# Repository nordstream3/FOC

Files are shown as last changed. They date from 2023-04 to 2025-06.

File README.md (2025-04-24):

# King of FOC motor control hardware aka FOC_KING

## The DIY Open Source Vesc6 and FOC capable HW with onboard IMU and CAN
<div>


</div>

IMAGE ALT TEXT (https://www.youtube.com/watch?v=1HfkBNfPIXc "FreeDRIVE")

Date | Manufacturer | amount | includes | shipping & tax | price
| -------- | -------- | -------- | -------- | -------- | -------- |
2024-01-17 | JLCPCB | 10 boards | All assembled excl fets and caps | YES, to EU | $241.08

An open-source motor controller board based on a JLCPCB friendly [VESC6 75V/300A](https://vesc-project.com/sites/default/files/Benjamin%20Posts/vesc_75_300.pdf) so-called "driverless" design with individual gate drivers for all three phases. It is powered by an STM32F405 MCU and is capable of running FOC at high power and voltages.

A motor controller designed for FOC (Field Oriented Control) and HFI (High Frequency Injection), a sensorless teqnique enabling full torque at zero speed without sensor feedback. The hardware is separated in 3 sub-modules which are assembled using standard pin headers.

POWER BRIDGE | MCU | SUPPLY
|----|----|----|
 |  | 
3 phase power bridge | STM32F405 PILL | +12,+5V,+3V

Intended for "small" electric vehicles like Skateboards, OneWheels, Bicycles, Robotics, Boats, and is designed in sub-modules as a reference design for further development.

The standard design includes 12 mosfets, but it will also work with just 6 fets. You choose.

## Features
* 84V/200A continuous rating
* 20s battery voltage rating
* 3-phase FOC motor control
* 4-layer pcb design with individual gate drivers for all three phases
* STM32F405 MCU
* USB-C
* CAN, 5 mbps
* Onboard IMU (Bosch BMI270)
* Momentary on/off switch connection via 4-pin jst connector
* Led data pin for programmable LEDs
* Compact design with fets mounted on the bottom side
* 12V for gate drivers, 5V for CAN and IMU, and 3.3V for MCU and op-amped current-sense amplification
* Cheap and up-to-date with cheapest and **well stocked** components available for ordering at [JLCPCB](https://jlcpcb.com/) and [LCSC](https://www.lcsc.com)
* **Dimensions of assembled board: 65 x 78 mm**

<div>
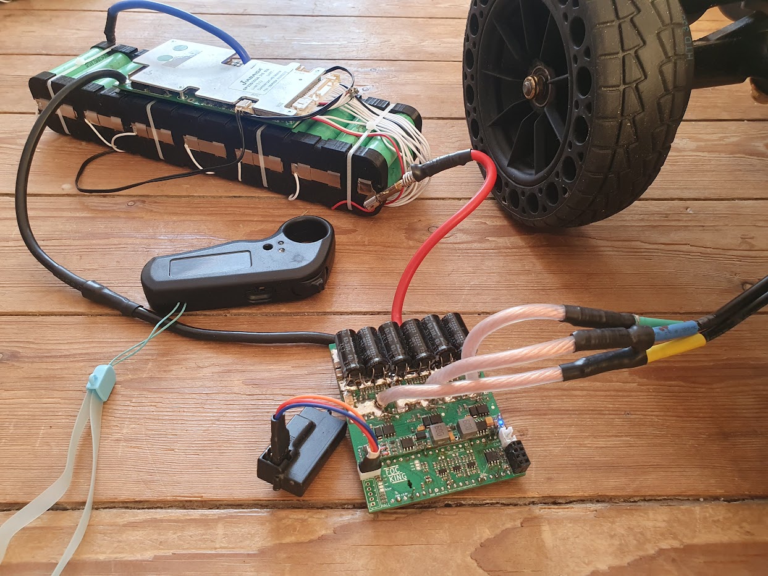
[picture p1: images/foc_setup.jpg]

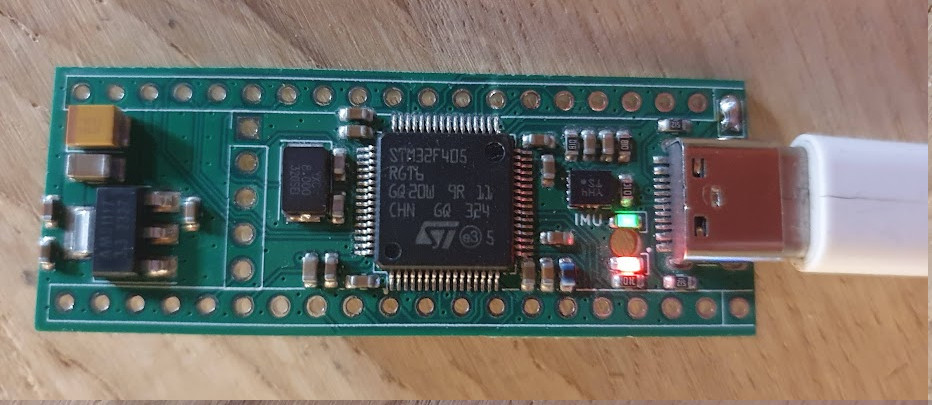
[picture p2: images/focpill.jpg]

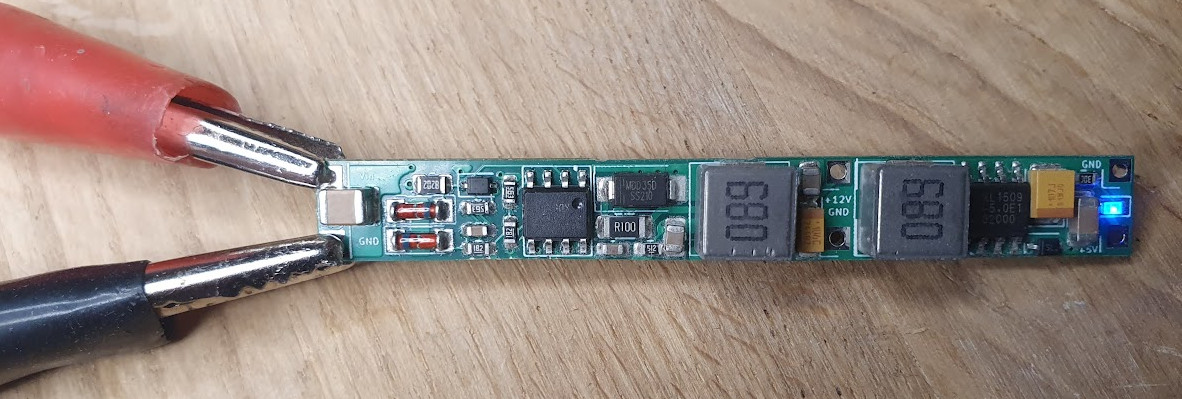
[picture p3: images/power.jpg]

</div>

<div>
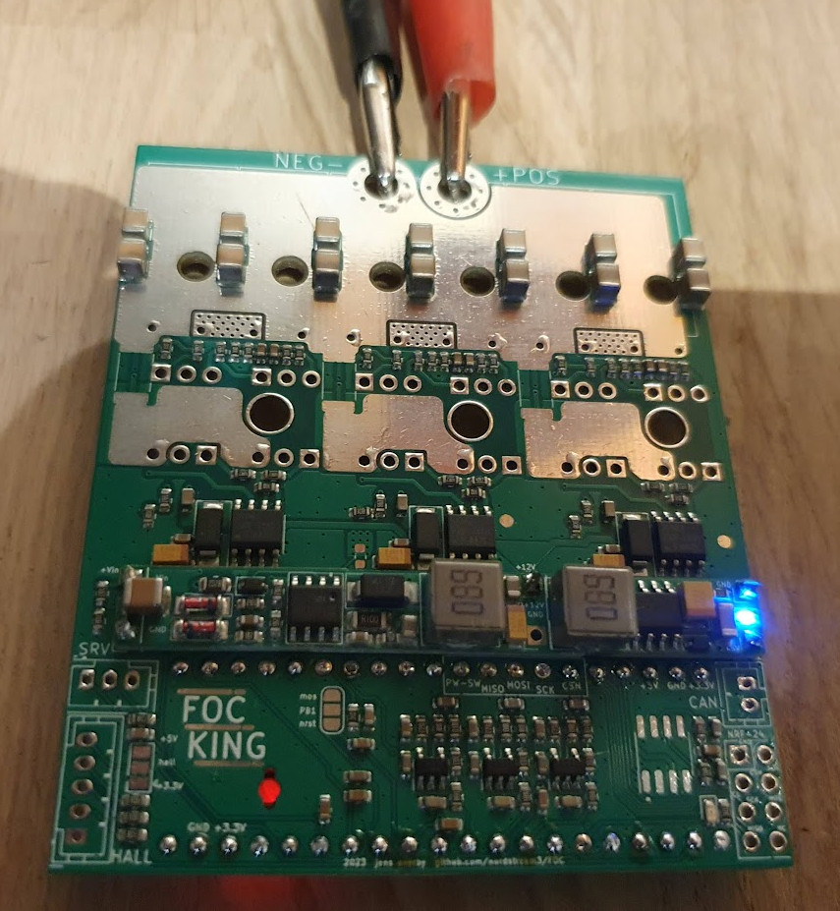
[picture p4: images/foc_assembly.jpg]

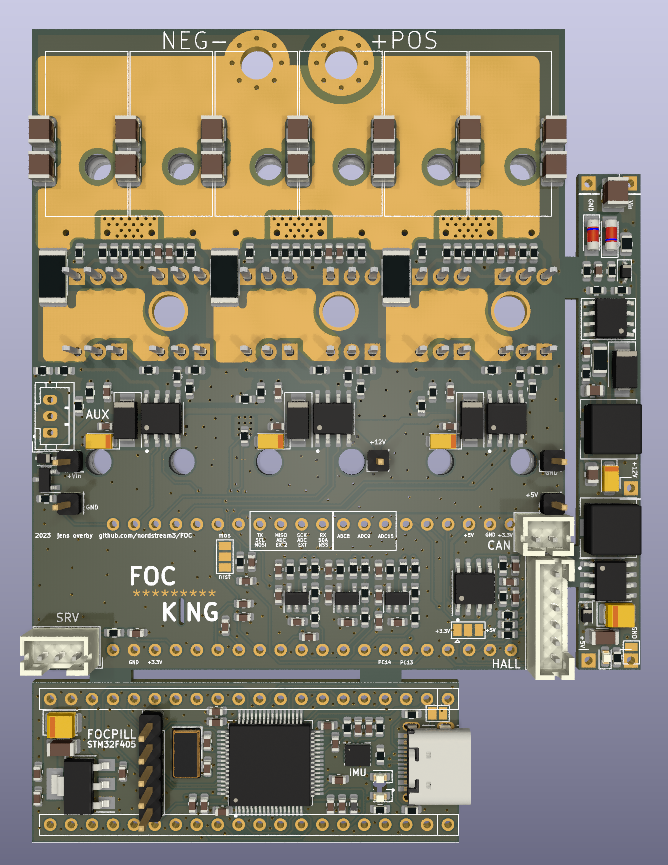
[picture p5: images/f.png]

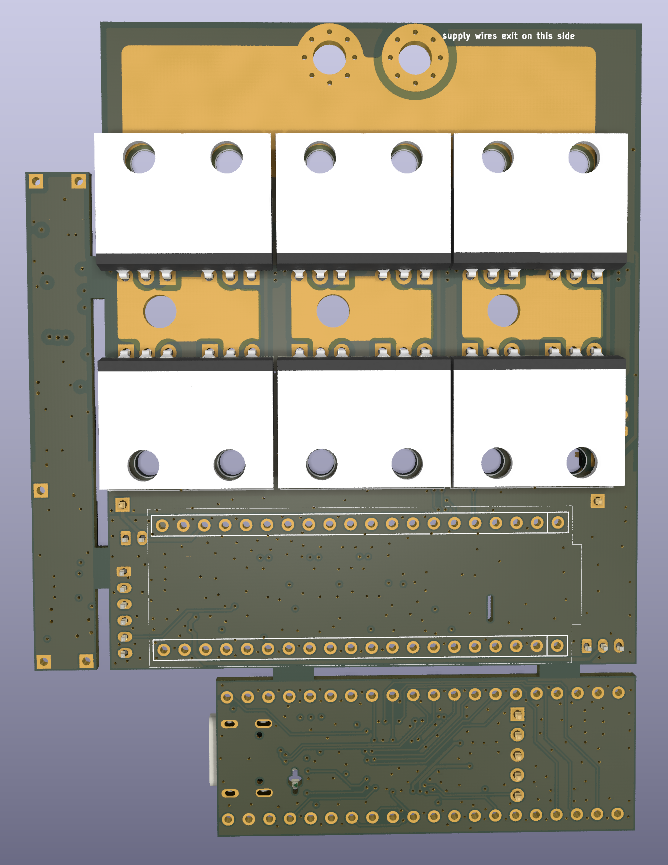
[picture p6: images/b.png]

</div>

[FOC_KING thread on esk8](https://forum.esk8.news/t/f-of-c-open-source-free-of-charge-vesc6-board-in-development-schematics-available/74888/277)

Advantages of separation into modules?
* Suitable for further development by DIY people
* Compatibility with other FOC projects
* Understanding of FOC HW is easier
* HW development is cheaper
* Debugging is easier

Disadvantages
* Assembly takes longer time. You need to solder 46 pinheader pins manually

## How to order at JLCPCB.COM

In the /production folder there is a guide for the [ordering procedure](./production/ordering_guide.md).

## How to assemble

Below is an image of the whole kit needed for assemble. The guide for the [assembly procedure](./production/README.md) is in the /production folder.



## Usage
Use the [VESC Tool](https://vesc-project.com/vesc_tool) to configure the motor controller according to your specific motor and application requirements.

## Contributions
Contributions to this project are welcome and encouraged. If you have any suggestions or improvements, please open an issue or a pull request on the GitHub repository.

## Donate
If you find this project useful and would like to support bread-and-butter for very time consuming development and maintenance, you can [donate 1$](https://www.paypal.com/donate/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) to the creator via [PayPal](https://www.paypal.com/donate/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).
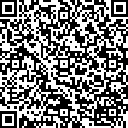
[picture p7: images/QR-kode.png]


## License
FOC_KING is released under the CERN Open Hardware License (OHL), developed by the European Organization for Nuclear Research. In short, it is a permissive license that allows anyone to use, modify, and distribute the licensed hardware, as long as they provide attribution to the original creators and distribute their modifications under the same license.

## Acknowledgements
FOC_KING is built on the work of the [VESC project](https://github.com/vedderb/bldc) and the contributions of its developers and contributors. Many thanks to *mxlemming* (aka [David Molony](https://github.com/davidmolony/MESC_FOC_ESC)) and *crinq* on the vesc forum on discord for their careful review and advice. Also this project is inspired by the format and concept of the [MP2](https://github.com/badgineer/MP2-ESC) by *badgineer* and the [Cheap Focer2](https://github.com/shamansystems/Cheap-FOCer-2/blob/Developer-Branch/README.md) by *shaman*.

><sub>[markdownguide.org/basic-syntax](https://www.markdownguide.org/basic-syntax/)</sub>  
><sub>[www.markdownguide.org/hacks/](https://www.markdownguide.org/hacks/)</sub>  
><sub>[support.squarespace.com Markdown-cheat-sheet](https://support.squarespace.com/hc/en-us/articles/206543587-Markdown-cheat-sheet)

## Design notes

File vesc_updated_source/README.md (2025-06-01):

Apply the Patch

On the target system, ensure you have a copy of dir_original (e.g vesc v. 6.05) and apply the patch using patch:

patch -p2 -d dir_original < updates.patch

example:
patch -p2 -d ./bldc-release_6_05 < vesc_foc_king20_bmi270.patch

Explanation:
-p2: Strips the first level of directory from the paths in the patch.
-d dir_original: Changes to the directory where the patch should be applied.

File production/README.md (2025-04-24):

# Assembly Guide



Wauw, it looks cool, but unfortunately something has gone wrong in this assembly.

What we want to build here will look something like this:



> (This is an image of an old version) The 3d printed enclosure you can find in the /production folder as obj files. You don't necessarily need an enclosure, but it will protect the components from short circuits etc.

For a complete assembly of the board you will need:



Pcs | Part | LCSC order no.
| ----- | ----- | ----- |
1 | Pre-assembled pcb
85 | Machine header pins (1 lot of 5pcs 2.54mm Pitch 1x40) | [AliExpress](https://www.aliexpress.com/item/1005005053790061.html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)
6 or 12 | Mosfets of type CRST030N10N | C841369
2 | 680uF Aluminum Electrolytic Capacitors D10xL25mm | C443095
3 | Female banana bullet connectors | C99865
1 | XT90H-M Male battery connector | C3040683
1 | JST	1x2P 2 pin JST (p=2.0mm) | C7465567
1 | JST 1x6P 6 pin JST (p=2.0mm) | C7465571
x | Cables

Additionally, you might need:
Pcs | Part | LCSC order no.
| ----- | ----- | ----- |
6 or 12 | Mica Insulation Sheet | Aliexpress
6 or 12 | White Insulation Washer TO-220 | Aliexpress
6 or 12 | M3 Stainless Steel Allen Bolts and Screws | Aliexpress
x | Aluminum for sinking heat
x | 3D printed enclosure (production folder)

> The board is produced by the manufacturer as a single pcb. JLCPCB will charge you for the number of designs on a pcb, but this is a single design where the modules are going to be assembled to a single unit. The separation is just for convenience purposes and none of the modules will work on their own.

The 3 modules are connected by taps, and you separate these using a suitable manual saw. Be careful not to damage the traces on the PILL and POWER modules in particular, as the traces here are close to the edges.

<div>

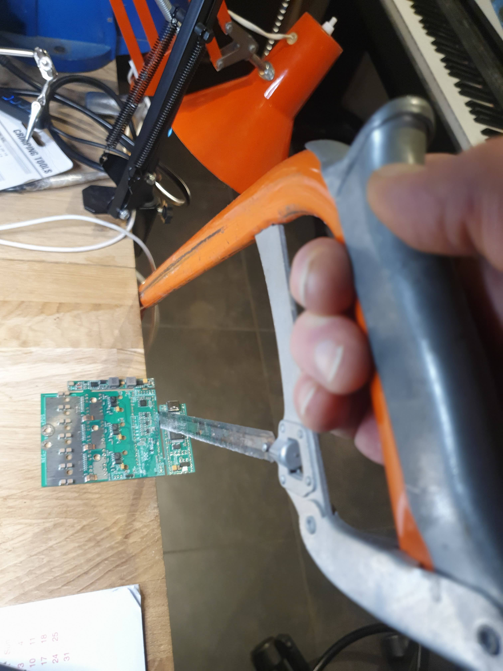
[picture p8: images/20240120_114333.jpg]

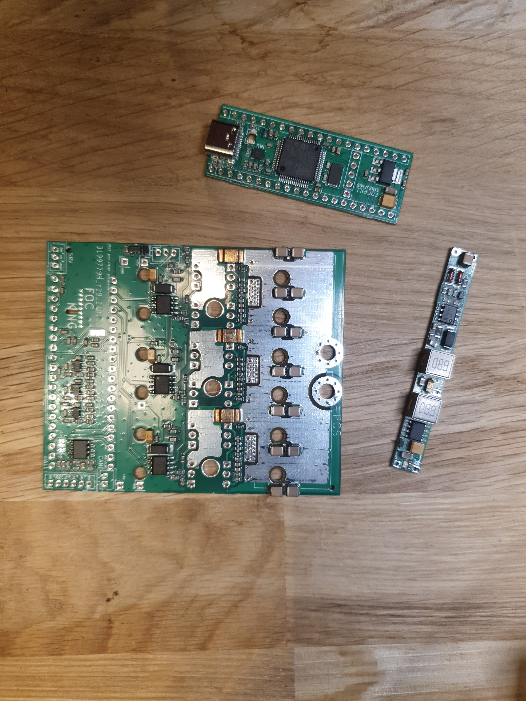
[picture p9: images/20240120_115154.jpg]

</div>

You should straighten the edges of the separated modules with sandpaper or a file.

## How to avoid creating solder bridges and other errors by testing throughout the Assembly Procedure
> Any error that you accidentally introduce to the board is really not a big deal, as long as you catch the error early on. This is why it is very important to verify the hardware after each step in the assembly.

Test or you will regret that you didn't!
| -------- |

## Step 1: Uploading Firmware and testing the PILL

The Pill can be powered from USB +5V by temporarily bridging the two pads next to the USB-C connector.

<div>



</div>

Now, Connect the Pill via a USB-C cable to your computer.
In this example I use a STM32F4 Discovery board for uploading firmware, but there are other options available:

[Existing VESC hardware](https://www.youtube.com/watch?v=PFFiVxFHDM4&t=312s)

[stm32f4 Discovery](https://geekilyinteresting.wordpress.com/2014/05/04/using-your-stm32f4-discovery-board-as-a-programmer-and-debugger/)

[ST-LINK windows](https://www.youtube.com/watch?v=etglJKNJSCY)

[stlink-gui on Ubuntu Linux](https://www.youtube.com/watch?v=VhLIKFwoGjo)

<div>

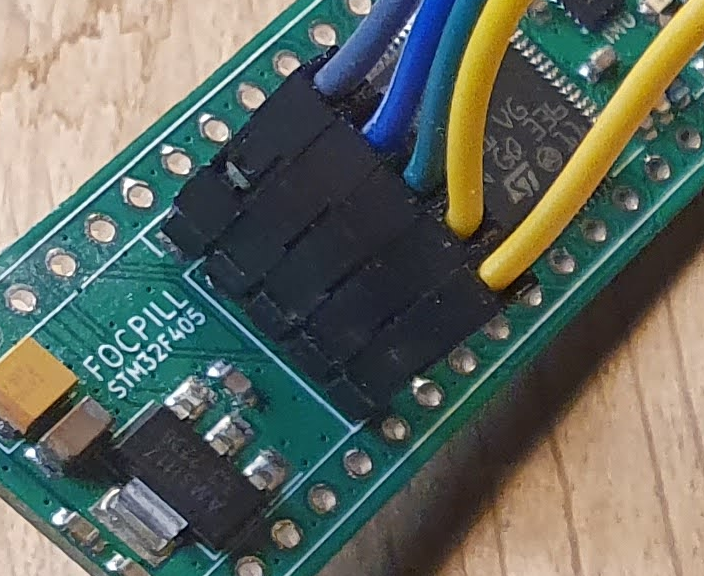
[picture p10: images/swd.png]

</div>

> There is no specific need for soldering pin-headers to the SWD terminals. Usually you only need a connection for a few seconds, and just applying a bit of tension to the terminals during the upload is enough. The pill is going to be soldered to the bottom side of the main module, and permanent pin-headers are not convenient on this side of the board.
>> The square pad on the pill SWD header is VCC (+3.3V).
>> 
>> In this example I use "stlink-gui" on Linux for uploading firmware. If you're on Widows or Mac use one of the other options.

Flash the bootloader to address 0x08000000. Bootloader can be found in the "binaries" folder.

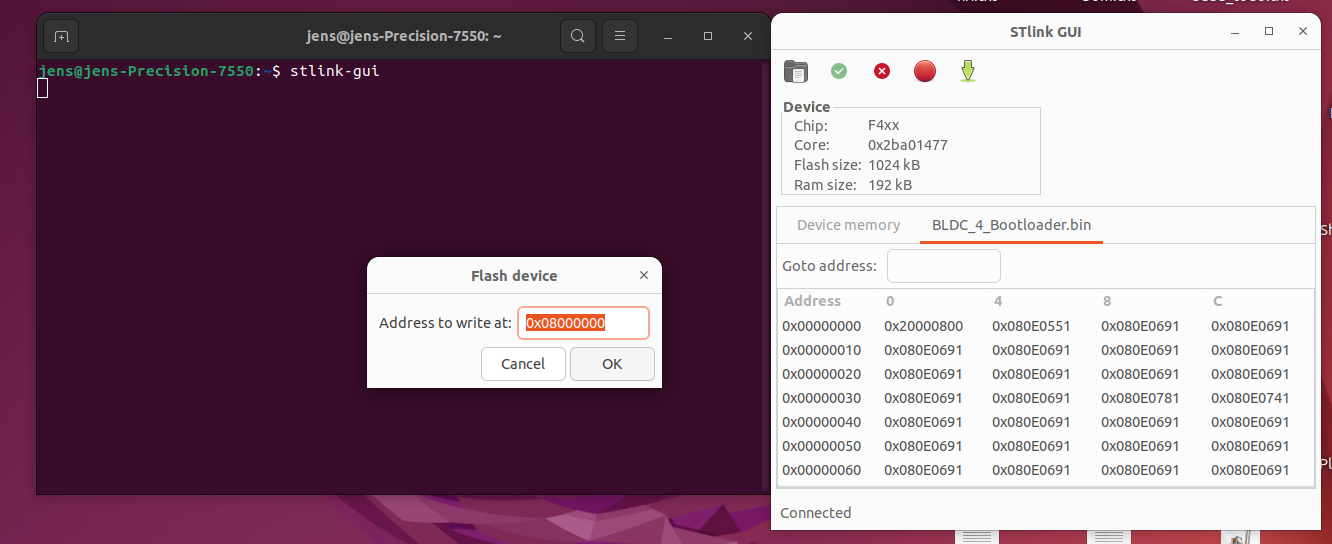
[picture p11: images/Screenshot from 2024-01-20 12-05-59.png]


Next, flash the Vesc firmware, also to address 0x08000000. Can also be found in the "binaries" folder.

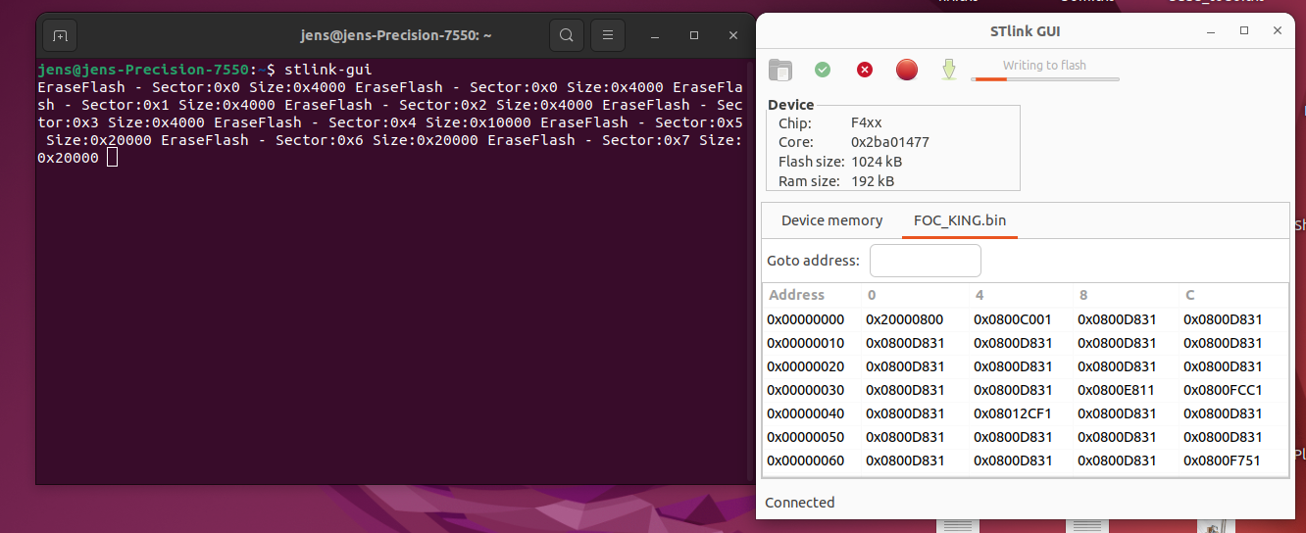
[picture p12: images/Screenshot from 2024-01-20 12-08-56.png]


Once you have flashed the firmware and the Pill is booted, the LEDs on the board will show a constant green light and a blinking red light. You should be able to discover the board in the Vesc Tool under the name "FOC_KING".

<div>

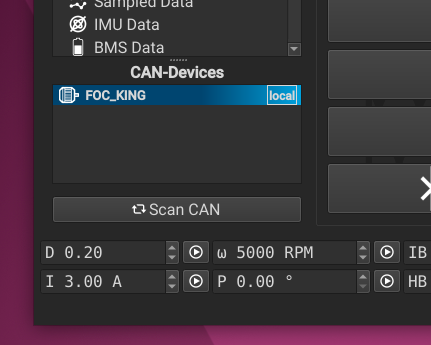
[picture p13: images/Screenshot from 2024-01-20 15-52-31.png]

</div>

**REMEMBER** to remove the solder bridge again. The assembled board will **NOT** work properly if powered by USB.
| ------- |
<div>
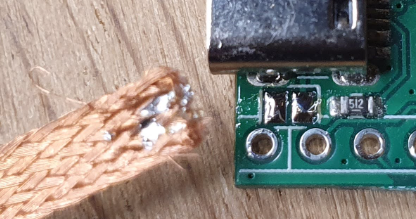
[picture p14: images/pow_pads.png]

</div>

## Step 2: Verify the POWER hardware

Connect the Power Module to a power supply as shown on the image below. Be VERY careful not to short the connections. Set the voltage to +16V with a **current limit of 0.1 Amps**.

<div>

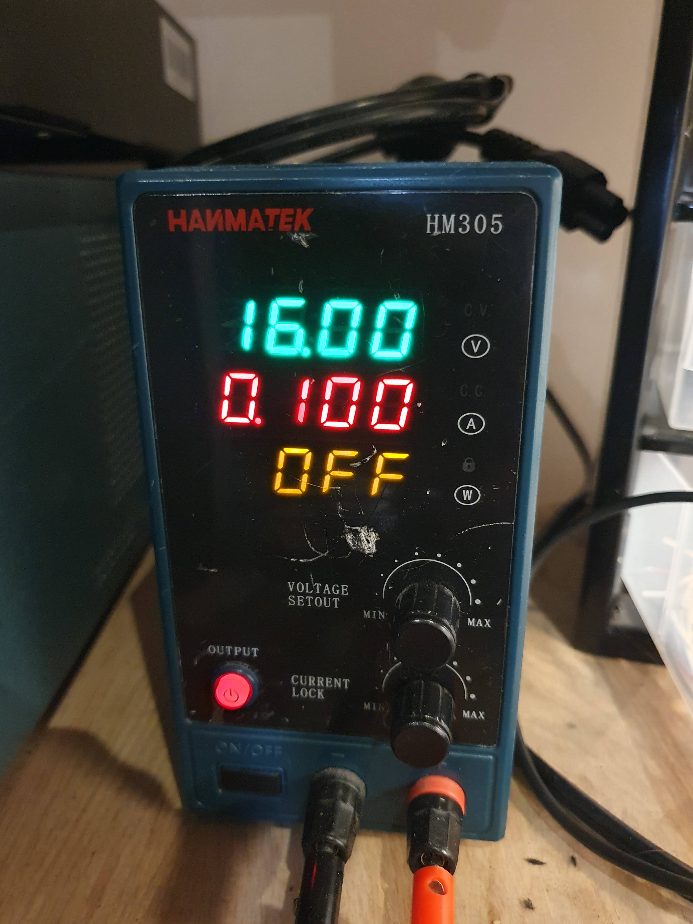
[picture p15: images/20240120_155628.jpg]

</div>

The module is working properly when the LED on the module shows a constant blue light.

## Step 3: Solder the Pill and Main Module together

Some JST connectors will overlap with the Pill at the terminals marked with red:

<div>

</div>

This is a challenge, because we are going to solder the Pill and Main Module together using standard pin headers. Because terminals are shared with JST connectors, we remove the pins of the JST sockets where there is overlap, and then the pin-header pins with replace these.

To end up with a proper JST-pin length, we need to pull out the pin-header pins around 1.5 mm at these spots.

<div>




</div>

Follow this procedure in this order:

1. With a set of pliers, on the standard pin headers, pull out the "shared" pins around 1.5 mm with reference to the black plastic spacer.
2. Solder pin headers to the Pill.
3. (Note: If you want to be able to desolder the two modules later, it's an advantage to remove the plastic spacers on the standard pin headers. By doing so, it's easier to apply heat to the pins so you can pull them out again)
4. Mount the Pill on the back side of the 'Main Module'.
5. On the front side of the Main Module, solder the Pill pins to the Main Module. Where you see cutouts for JST connectors, be VERY careful to apply only the slightest amount of solder, or else you will be in trouble when mounting the "plastic only" part of these JSTs later. The GND and +3V terminals will need a lot of heat. If too much solder is applied, you can scrape it off gently using a hobby knife.
6. Pull out JST pins of the JST sockets in those locations where they overlap with the pin-headers that you've already soldered.
7. Carefully, mount these sockets in their respective places on top of the respective pins (pin headers).



## Step 4: Solder power connector pins

Solder 5 power connector pins onto the Main Module.

<div>


</div>

You can now temporarily attact the Power Module to the Main Module. You can bend the pins slightly in order to secure a good connection. Do not solder the two modules together yet (until you have attached heat sinks to mosfets). You should be able to power the complete board by applying +16V across the main supply terminals. **Use a current limit of 0.1A**.

<div>


</div>

At this stage, the board should draw around 0.05A at 16V.

## Step 5: Apply solder to exposed copper planes

Apply around 0.3 mm of solder to the large exposed copper planes of both sides of the Main Module (however, not anything yet to the "phase" planes in between the mosfets).



> Putting a layer of solder on the planes is done for thermal management reasons rather than for enhancing electrical conductivity.
> Solder has better thermal conductivity than the bare copper, so adding a thin layer of solder can enhance the thermal performance further. This can help in better heat dissipation from the switching mosfets, which generate significant heat during operation.

## Step 6: Solder first 6 mosfets



Bending the caps at the right spot is an advantage, if you want to use the screw holes for mounting the heat sink.

> The screw holes for attachment of heat sink doesn't need to align up perfectly, but should not be too much off.



> You choose if you want to attach the remaining 6 mosfets. This obviously depends on the wattage spec you want of the board.

Power up the complete board by applying +16V across the main supply terminals. **Use a current limit of 0.1A**.



The board should obviously draw less than 0.1A - probably around 0.05A.

## Step 7: Solder the wires for main supply positive and negative. Also solder wires for all three phases



Attach a bldc motor to the three phase wires.

Again, apply the same test as in "Step 6"

## Step 8: Test the board when connected to a BLDC motor

If you were successful so far, connect all three phase wires of a BLDC motor to the board.

Increase the voltage to +24V and **set a current limit of 0.3A**.

Connect to "FOC_KING" in the Vesc Tool and go to the "Vesc Dev Tools" menu and type the command "help". This should give you a long list of available developer command line options.

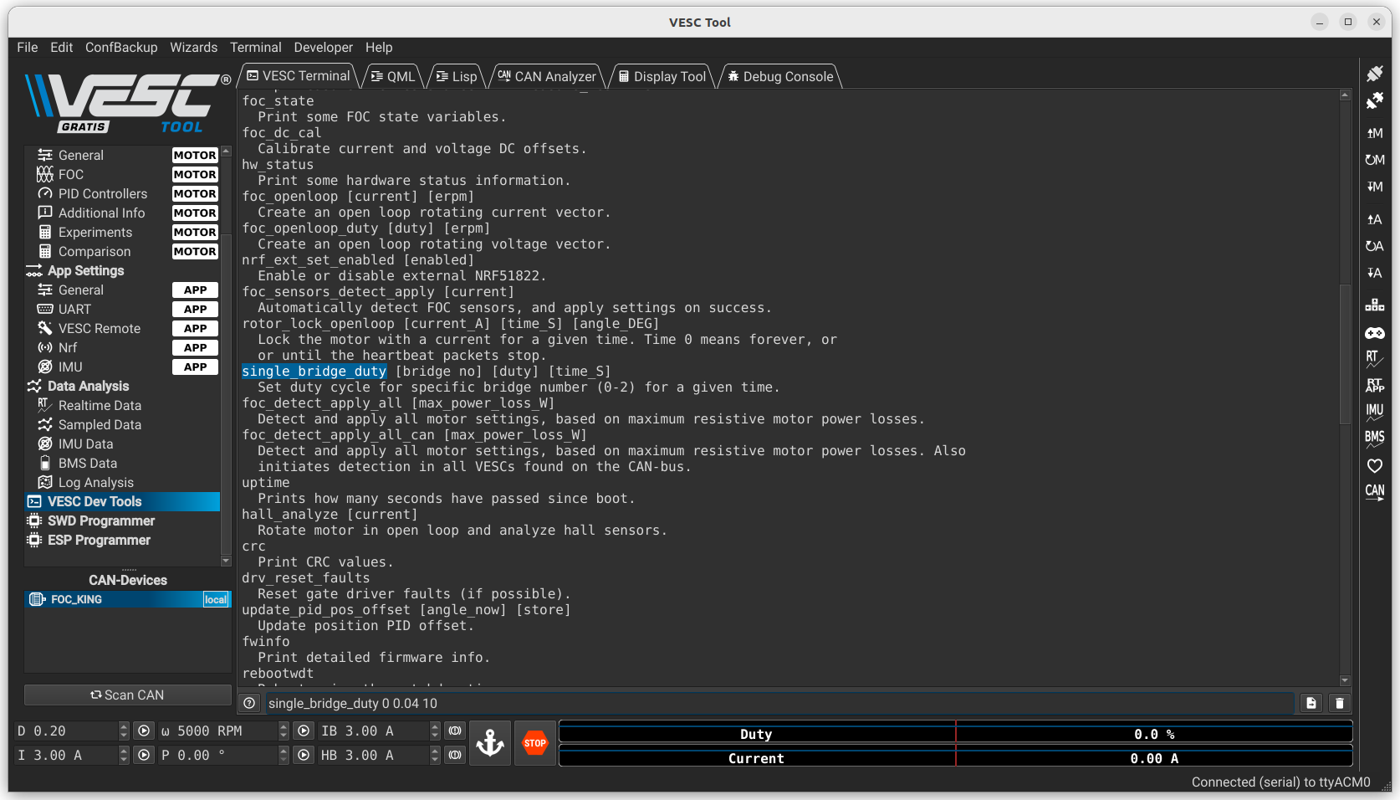
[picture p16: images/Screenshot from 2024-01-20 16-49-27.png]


Scroll up til you find the "single_bridge_duty" command (a very helpful command currently only available for the FOC_KING firmware).
Write the command:

```
single_bridge_duty 0 0.04 10
```

(which is equivalent to: Apply 4% duty cycle to phase no. 1 (index zero) for 10 seconds)

> If the drive completely shuts down now, or starts blinking. Did you remember to turn up the current to around 0.3A (possibly more for very large motors)?

If you try to turn the motor by hand now, you should feel some mechanical resistance. Note down the draw of current during this 10 second period.

If you run the same command for the two other phases, the draw of current should be around the same value. Also the felt mechanical resistance should be comparable. The commands for the two other phases are:

```
single_bridge_duty 1 0.04 10
```
```
single_bridge_duty 2 0.04 10
```

If something looks or feels odd in this procedure, maybe you accidentally bridged traces during soldering of mosfets?

If you open up the "Sampled Data" menu under "Data Analysis" and click on the "Sample Now" button, you should see something like this:

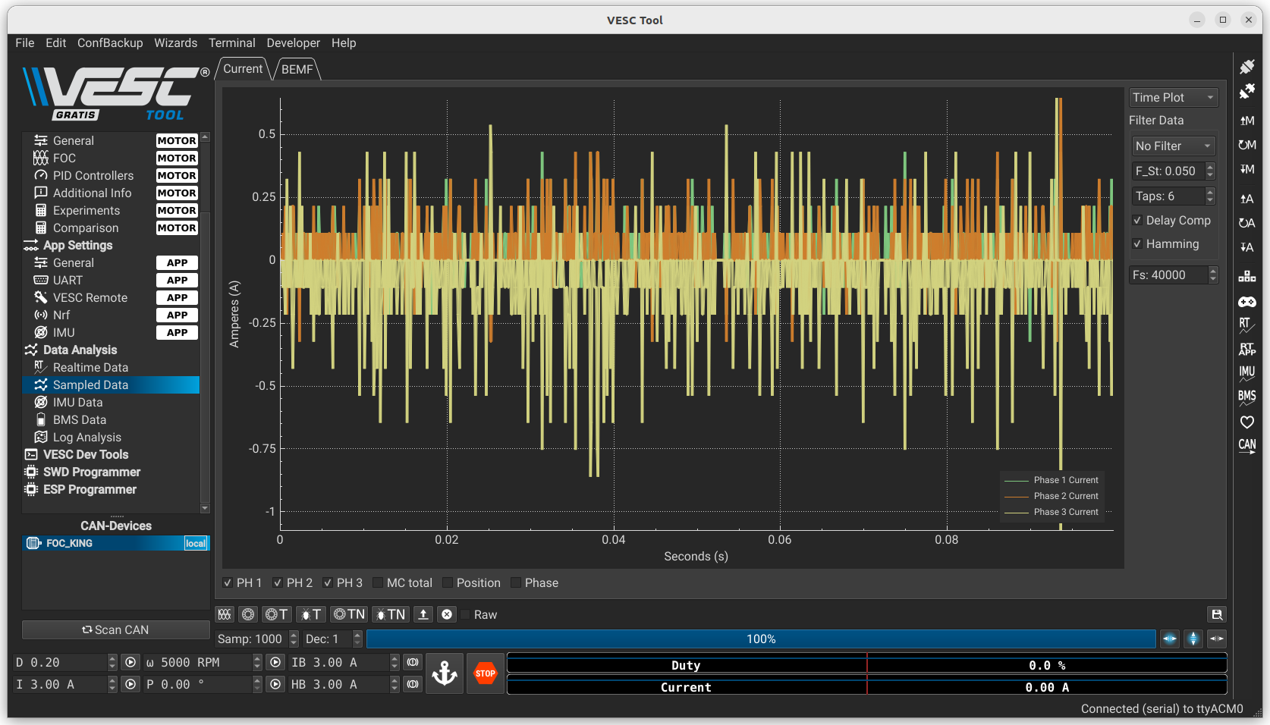
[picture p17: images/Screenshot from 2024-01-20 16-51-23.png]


All phase currents should be centered around zero.

If you lock a single phase for e.g. 20 seconds and do a current measurement during this period, you should see that the current of phase 1 stands out from phase 2 and 3
```
single_bridge_duty 0 0.04 20
```
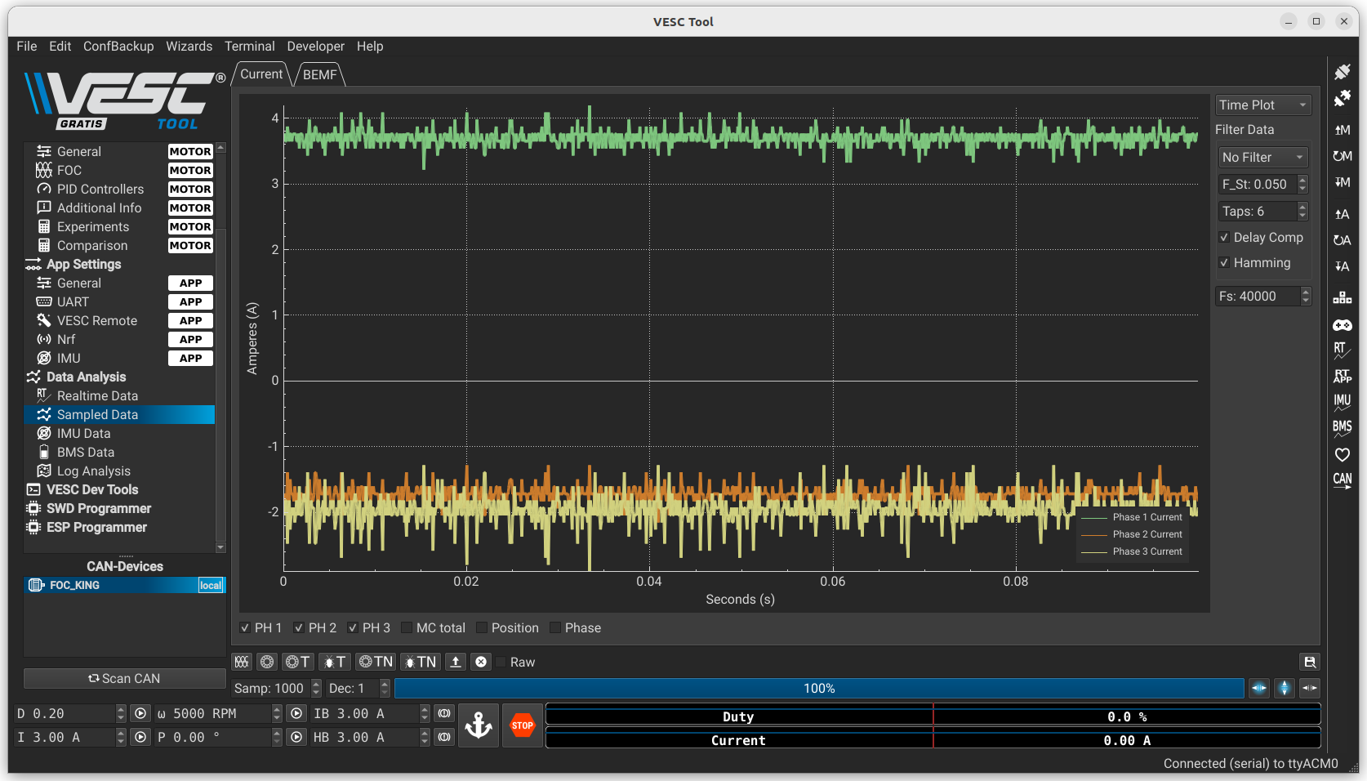
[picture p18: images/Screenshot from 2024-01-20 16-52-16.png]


Phase 2:
```
single_bridge_duty 1 0.04 20
```
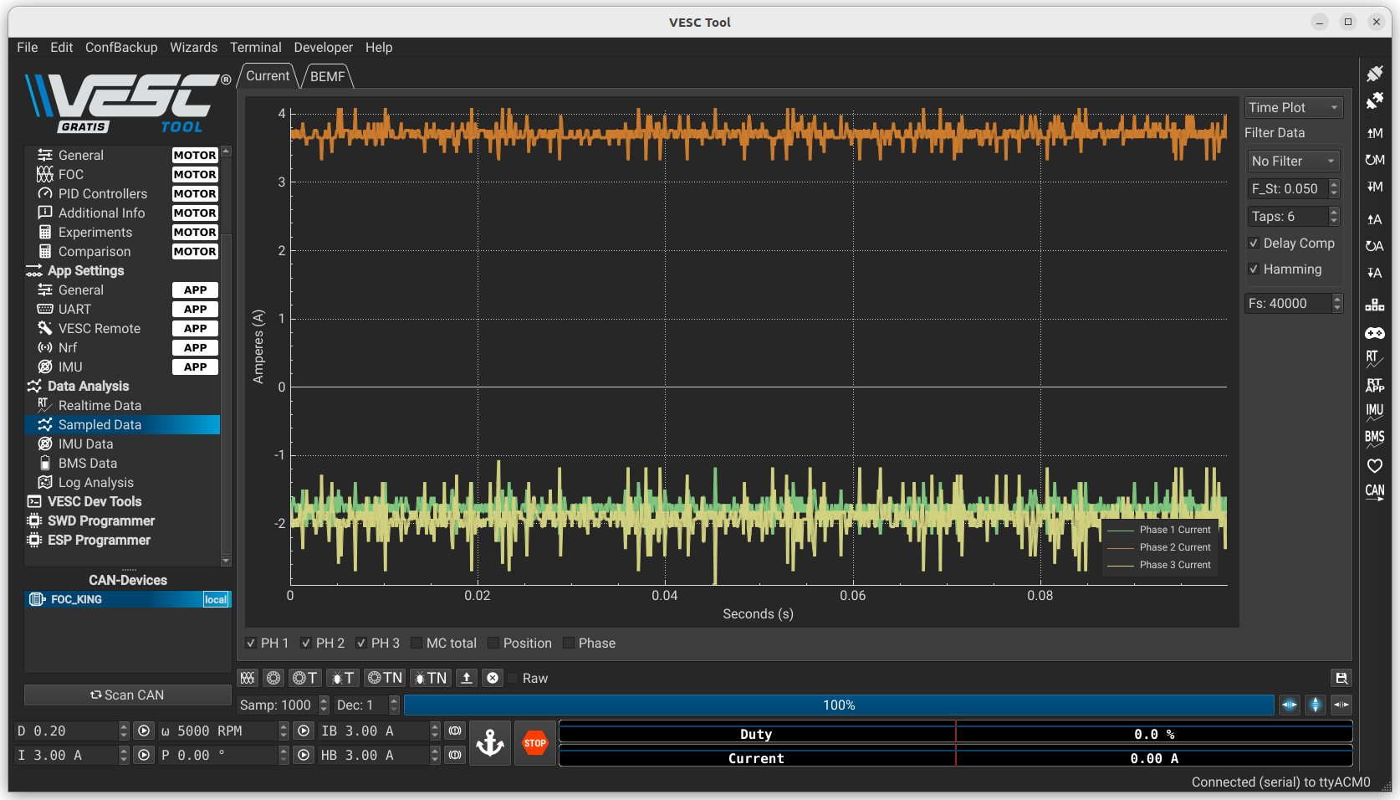
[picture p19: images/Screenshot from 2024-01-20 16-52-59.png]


Phase 3:
```
single_bridge_duty 2 0.04 20
```
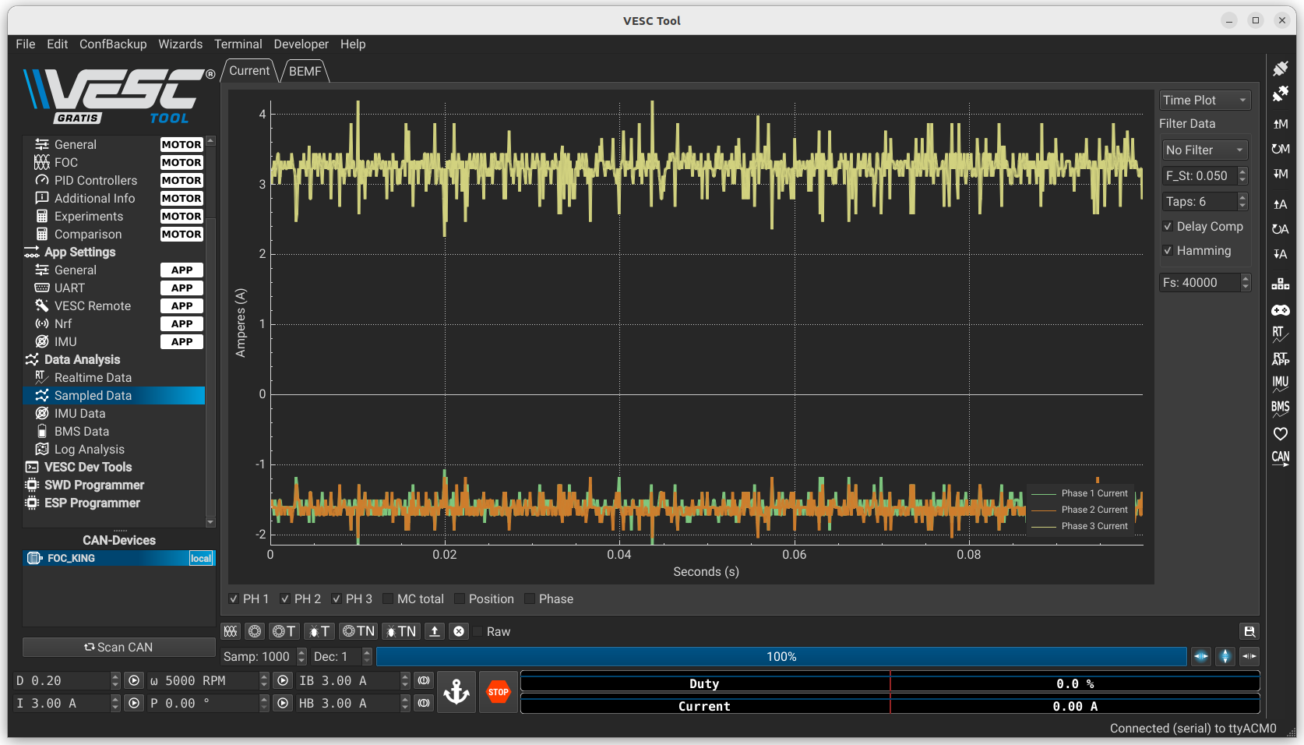
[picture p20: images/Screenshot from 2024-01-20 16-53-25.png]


## Step 9: Finish assembly by adding large capacitors or more fets

For better thermal management, apply a layer of solder to the top-side exposed copper planes.



> Don't use the amount of solder applied in this image as a reference. This is too much solder!

When mounting and soldering the 330uF capacitors, remember that the three small pads are positive V_in, and the large exposed copper plane is negative (GND).
<div>




</div>

The board is now assembled, and you can proceed to the normal procedure of "motor detection" in the VESC Tool.

If you want to 3D print an enclosure for your drive, you can find the .obj-files in the /production folder.

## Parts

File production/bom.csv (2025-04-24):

Designator | Footprint | Quantity | Value | LCSC Part #
C1 | 0603 | 1 | 4.7n | C53987
C10, C21, C34, C43, C5, C53, C6, C61, C62, C63, C66, C67, C69, C72, C74 | 0603 | 15 | 100n | C14663
C11, C15, C16, C19, C25, C27, C29, C33, C4, C42, C45, C52, C64, C65, C7 | 0603 | 15 | 2.2u | C23630
C12, C18, C2, C22, C3 | 0603 | 5 | 100p | C14858
C13, C23, C8 | 1206 | 3 | 100u@6.3V | C15008
C14, C20, C28, C75 | 0603 | 4 | 10u | C96446
C17, C24, C32, C9 | CP_EIA-3216-10_Kemet-I | 4 | 10u | C7171
C26, C36, C37, C38, C39, C46, C47, C48, C49, C55, C56, C57, C58 | 1210 | 13 | 4.7u 100V | C381466
C30, C70 | 0603 | 2 | 10n | C57112
C31 | 0805 | 1 | 22u | C45783
C35, C44, C54 | 0603 | 3 | 1n | C1588
C40, C41, C50, C51, C59, C60 | 0603 | 6 | 4.7n | C382251
C68 | 0603 | 1 | 1u | C15849
C71, C73 | 0603 | 2 | 12p | C38523
CYA0650-68UH1, CYA0650-68UH2 | L_6.6x7.2_H5.0_CYA0650_68UH | 2 | 68uH | C5189964
D1, D2, D4, D7 | D_SMA | 4 | US1M | C412437
D10 | 0805 | 1 | GREEN | C2297
D11 | 0603 | 1 | WHT | C2290
D3 | D_SOD-323 | 1 | 1N5819 | C191023
D5 | D_SOD-323 | 1 | 1N4148WS | C2128
D6 | D_SOD-123 | 1 | MM1W18 1W18V zener | C382948
D8 | D_SMA | 1 | SS210 | C14996
D9 | 0805 | 1 | RED | C84256
H1, H10, H11, H12, H2, H3, H4, H5, H6, H7, H8, H9 | MountingHole_3.2mm_M3 | 12 | MountingHole
H13 | MountingHole_3.5mm_Pad_TopOnly_custom | 1 | Phase_A_Pad
H14 | MountingHole_3.5mm_Pad_TopOnly_custom | 1 | Phase_B_Pad
H15 | MountingHole_3.5mm_Pad_TopOnly_custom | 1 | Phase_C_Pad
J1 | JST_PH_B2B-PH-K_1x02_P2.00mm_Vertical | 1 | Conn_01x02_Male
J2 | JST_PH_B6B-PH-K_1x06_P2.00mm_Vertical | 1 | Conn_01x06
J3 | JST_XH_B6B-XH-A_1x06_P2.50mm_Vertical | 1 | communication
J4 | JST_PH_B4B-PH-K_1x04_P2.00mm_Vertical | 1 | on/off
J5 | JST_XH_B4B-XH-A_1x04_P2.50mm_Vertical | 1 | servo
J6 | HRO_TYPE-C-31-M-12 | 1 | TYPE-C-31-M-12 | C165948
L1 | 0805 | 1 | 10n | C1046
NT1, NT2, NT3, NT4, NT5, NT6 | NetTie-2_SMD_Pad0.5mm | 6 | NetTie_2
P1, P10, P12, P13, P2, P3, P4, P5, P6, P7, P8, P9 | PinHeader_1x01_P2.54mm_Vertical | 12 | SWD
P11 | PinHeader_1x05_P2.54mm_Vertical | 1 | SWD
Q1 | SOT-23 | 1 | AO3401A | C15127
Q10, Q11, Q12, Q13, Q14, Q15, Q4, Q5, Q6, Q7, Q8, Q9 | TO-220-3_Vertical_bend | 12 | CRST030N10N | C841369
Q16, Q2, Q3 | SOT-23 | 3 | SS8050 | C2150
R1, R11, R15, R17, R19, R2, R28, R3 | 0603 | 8 | 2k | C22975
R10, R50, R7, R88, R89 | 0603 | 5 | 10k | C25804
R12 | 0603 | 1 | 470k | C23178
R13, R26, R6, R86, R87 | 0603 | 5 | 5.1k | C23186
R14, R16, R18, R22, R23, R27, R38, R41, R58, R61, R76, R79 | 0603 | 12 | 56k @ 75V | C23206
R20 | 0805 | 1 | 82k @ 150V | C17840
R21, R24 | 0603 | 2 | 1k8 | C4177
R25 | 1206 | 1 | 0.1R | C25334
R29, R47, R67 | 0603 | 3 | 150R | C22808
R30, R49, R68 | 0603 | 3 | 30k | C22984
R31, R32, R43, R44, R45, R46, R51, R52, R63, R64, R65, R66, R69, R70, R81, R82, R83, R84 | 0603 | 18 | 10R | C22859
R33, R92, R93 | 0603 | 3 | 56k | C23206
R34, R35, R54, R55, R72, R73, R96, R97 | 0603 | 8 | 1k | C21190
R36, R37, R39, R40, R56, R57, R59, R60, R74, R75, R77, R78 | 0603 | 12 | 4.7R | C23164
R4, R5, R85 | 0603 | 3 | 100R | C22775
R42, R62, R80 | 2512 | 3 | 0.25mR | C495759
R48 | 0603 | 1 | NTC 10k | C13564
R53, R71, R91 | 0603 | 3 | 6.2k | C4260
R8, R9 | 0603 | 2 | 75k | C23242
R90 | 0603 | 1 | 20k | C4184
SW1, SW4 | SolderJumper-3_P1.3mm_Bridged2Bar12_Pad1.0x1.5mm | 2 | SW_SPDT
SW2, SW3 | SolderJumper-2_P1.3mm_Open_Pad1.0x1.5mm | 2 | SW_SPST
U1 | SOIC-8_3.9x4.9mm_P1.27mm | 1 | TJA1051T/3/1J | C38695
U10, U11 | TSOT-23-5 | 2 | MS8311
U12, U13 | Blackpill_STM32F401CEU6 | 2 | STM32F401CCU6_Blackpill
U14 | LQFP-64_10x10mm_P0.5mm | 1 | STM32F405RGT6 | C15742
U2 | Bosch_LGA-14_3x2.5mm_P0.5mm | 1 | BMI270 | C2836813
U3 | SOT-223-3_TabPin2 | 1 | AMS1117-3.3 | C6186
U4, U6, U7 | SOIC-8_3.9x4.9mm_P1.27mm | 3 | IRS21867S | C52290
U5 | SOP-8_3.9x4.9mm_P1.27mm | 1 | XL1509-5.0E1 | C61063
U8 | TX4130L_ESOP-8 | 1 | TX4130L/PW2902 | C448635
U9 | TSOT-23-5 | 1 | MS8311 | C1509000
Y1 | Crystal_SMD_5032-2Pin_5.0x3.2mm | 1 | 8MHz Crystal Resonator, X50328MSB2GI | C115962

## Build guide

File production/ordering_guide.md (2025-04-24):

# Ordering Guide

Follow [this](./gerber.zip) link to download the gerber zip file located in the /production folder.

Follow [this](https://cart.jlcpcb.com/quote) link to go to the upload of Gerber Files at jlcpcb.

When the gerbers are uploaded, you should see this:



Choose the decired **pcb quantity**. Minimum quantity is 5.

Leave all the other choices at their default, and scroll to the bottom of the page:


Select "Free Assembly for your PCB order".



Again, you need to specify the how many of you ordered pcbs you would like to be pre-assembled with components.

Leave the remaining choices at their defaults and scroll to the bottom of the page and click "Confirm".

## Process BOM & CPL

After your confirmation, you will be presented with a kind of Wizard, with the first page showing a top view of the pcb.

Click "Next" to go to the relevant page for upload of BOM and CPL files.



Follow [this](./bom.csv) link to download the BOM located in the /production folder.  
Follow [this](./foc_cpl_top.csv) link to download the CPL located in the /production folder.

When you have successfully uploaded the BOM and CPL click on "Process BOM & CPL", whereafter you will be presented with an "ERROR".



Which is in fact not an error, but a notice that there is a mismatch between BOM and CPL, since the CPL only contains coordinates of components on the **top side** of the pcb. 

Importantly, you should click on "Continue", and you will presented with a **long** list of all the components matched in the BOM & CPL.

Scroll down the list to find if there are any components that fall short:


> This is just an example! There might not necessarily be any shortfalls.  
> FOC_KING is optimized for lowest jlcpcb price. Where possible, **basic library** is always first choice.  
> Basic Library: These are the components pre-loaded in the SMD Automatic Pick and Place Machine.  
> Extended Library: These are the components requiring manual setup, and you will be charged an extra fee per component type.

After you have found replacements for any shortfall components, you should scroll to find the "Connector_PinHeader_2.54mm footprints:


Importantly, you must **deselect** all 2.54mm pin headers.

When this is done, choose "Next", and you will be presented with a dialog:



Select "Do not place".

## Fix component rotational misalignments

You should now be presented with a rough render of the smd layout, where you need to fix a few issues by using the "rotate left" and "rotate right" buttons in the top menu.



These might be issues (but there could potentially be more):

Image | Components | To Do
|----|----|----|
 | 3 Shunt Resistors | Rotate all three so they lign up like this
 | 3 Gate Drivers | Rotate all three so white and cyan dots lign up
 | CYA0650-68UH2 | Nothing. Image missing, but OK
 | CAN Driver | Rotate so white and cyan dots lign up
 | 3 Op Amps | Rotate all three so legs match pads
 | IMU | Rotate so white and cyan dots lign up

## Overview of fixed smd layout

When the alignment issues are solved, the rendered smd layout should look something like this:



## Finalizing

Finally, you will be presented with an overview of price and build time.



Click on "Save to cart".

Your order is now added to your Shopping Cart, and you should **proceed to payment**.

## Remember to order the remaining components that you need to manually solder
* Mosfet
* 2 680uF Capacitors
* 4 1x20 Machine header pins
* JST Connectors
* etc.

These components are listed in the [Assembly Guide](https://github.com/nordstream3/FOC/edit/main/production) with LCSC part numbers and AliExpress links.

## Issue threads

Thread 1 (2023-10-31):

Cut GND islands under buck converters

ZantaHub, 2023-10-31:
Hi,

I saw that there was already some discussion in the esk8 forum about GND islands.

In the latest design the buck converters are still on GND islands and the current return paths (especially for the 5V regulator) are quite long.

Is there any reasoning behind this? Is this subject to change?

In my experience cutting GNDs like this almost always degrades signal quality.

Really like the project so far, keep it up!

nordstream3, 2024-01-03:
Hi.
This is interresting, and sorry for the late response. Now it indeed has become an island, because it is separated on power supply board. I'm learning electronics so I'm very happy about your feedback. The reasoning was that I've seen "somewhere" that you should connect ground of a buck converter at a "single point" - which I have interpreted as having a ground island for the buck. You think it's a better idea to just have a common ground? Could you guide me to a forum or Youtube video with discussion about this topic, if it is a topic?

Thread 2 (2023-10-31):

List of tasks to do?

saosebastiao, 2023-10-31:
Hi, this project sounds really interesting and I'm looking forward to see where it goes. I'd love to be able to contribute, would you have a list of tasks that need to be done to get this to an official release? It might help with contributions.

I notice that the BOM does not have LCSC parts numbers for some items, but some of them look fairly easy to look up. For example, the STM32F405RGT6 can be [found here](https://www.lcsc.com/product-detail/Microcontroller-Units-MCUs-MPUs-SOCs_STMicroelectronics-STM32F405RGT6_C15742.html) as C15742. Is this a task that can be farmed out? Or are you still working on the design and don't have parts in mind yet?

nordstream3, 2024-01-03:
Sorry for not answering this before now. The board is very close to a release now. Will try to do a TODO list for next release.

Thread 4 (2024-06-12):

Please make it suitable for higher voltage

LencoSolutions, 2024-06-12:
I guess the title says it all. I think we need at least 20s...

Bazing89, 2024-06-14:
Change the capacitor to a 100-volt capacitor to handle 20s. the recommended mosfets are already 100v. I believe that should work as its only 8 volts; the whole motor controller does not have to be redesigned.

shambler123, 2024-07-31:
Its working with 20s I am using it in a VESC OneWheel. Here is the Config file for 20s

https://github.com/shambler123/free-drive-20s

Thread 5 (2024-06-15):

CANBUS stops working..

Sylvania2, 2024-06-15:
Hi

I am using the canbus to access a total of 4 FOC's (terminations resistors removed from two boards). The 4 FOC shares the same 10S LIFEPO4 battery, there is no "ground" loops yet (Servo PPM input is not connected but gnd will be shared if connected to the controller board when connected). I can run the FOC wizard and control each unit through servo ppm). But then all Canbus units disappear while tuning the setup. I thought well maybe the TJA1051T/3 was defect and replaced it with a spare FOC. All fine, Canbus working. Then i exchanged the FreePILL board (with the one from the defect FOC) to test if it was the Canbus chip or the FreePILL board, error is back. So the FreePILL board canbus tx/rx pins is dead. Did a second test, USB connected to another FOC, this one also died after some time. So far it seems that Canbus dies on the FOC connected to usb.
I haven't found the cause of this error yet.

Board V1.0.0

Best regards

Sylvania2, 2024-06-24:
Setup failure ! 3 out of 4 vesc with same canbus id :-)

Closed 2024-06-24.

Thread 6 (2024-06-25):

Make gap between FETs wider.

steve2211, 2024-06-25:
Hello everyone,

This is an excellent project! I have already built 5 functional ESCs. The only problem I encountered was a short circuit between the drains of the FETs across the phases. This is only a concern when all 12 FETs are in use. I managed to resolve this issue by using small pieces of Kapton Tape, but it would be much more convenient if the FETs were spaced further apart. I believe a distance of 1mm should be sufficient.

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

Let me know if you need further information.

Thank you very much
Kind Regards

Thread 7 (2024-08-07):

Fix issue with push-button turn-on turn-off

nordstream3, 2024-08-07:
Reported by shambler to be unreliable.

I think a redesign of this small circuit is necessary. And probably it would be a good idea to integrate it with the Vesc, so "automatic" shutdown is an option.

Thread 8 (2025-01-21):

Update assembly instructions for 1.0 release

msprengholz, 2025-01-21:
Hi,

thanks for the nice project! I just got around to building my first working FreeDrive. Sadly, I probably killed my first board because I was not careful enough while following the assembly guide. I guess this is also due to the outdated pictures in the assembly guide. I could figure it all out with a picture from #6 that showed the correct mounting position for the FreePill. To spare others my mistake I have made some updated pictures of the assembly process that I would like to share here:

## flashing

Connect all five cables as shown. The square pinhole is VCC.
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
The pin order for reference:
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

## soldering pins to FreePill

The pins point upwards. Pins are pulled out further where JST connectors are drawn in silkscreen on the main module (as is explained in the assembly guide)
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

## mounting of power module

The power module is placed on the other side compared to the FreePill. It is also mounted upside down. I first soldered the pins to the power module and then later to the main module.

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

## almost fully assembled

FreeDrive is working. It is only missing the JST connectors.

front:

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

back:
Mounted power module and Freepill. Soldering of 6 FETs and attached motor cables.

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

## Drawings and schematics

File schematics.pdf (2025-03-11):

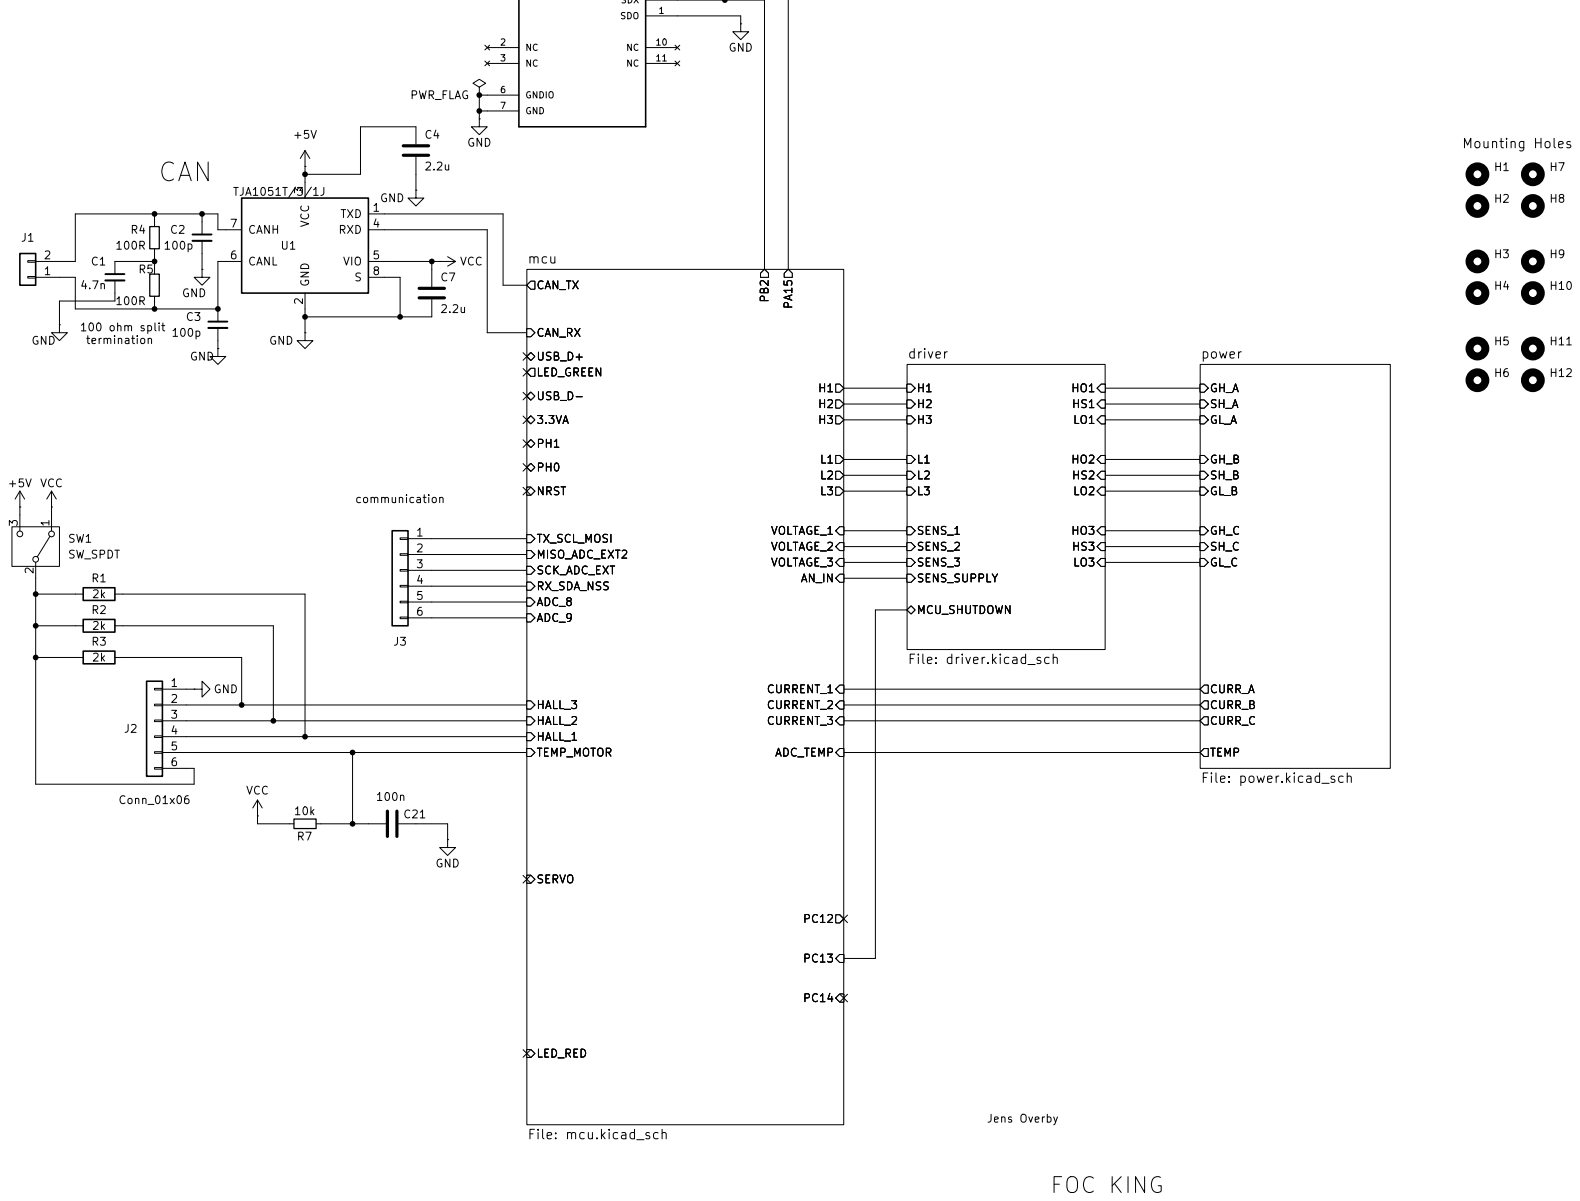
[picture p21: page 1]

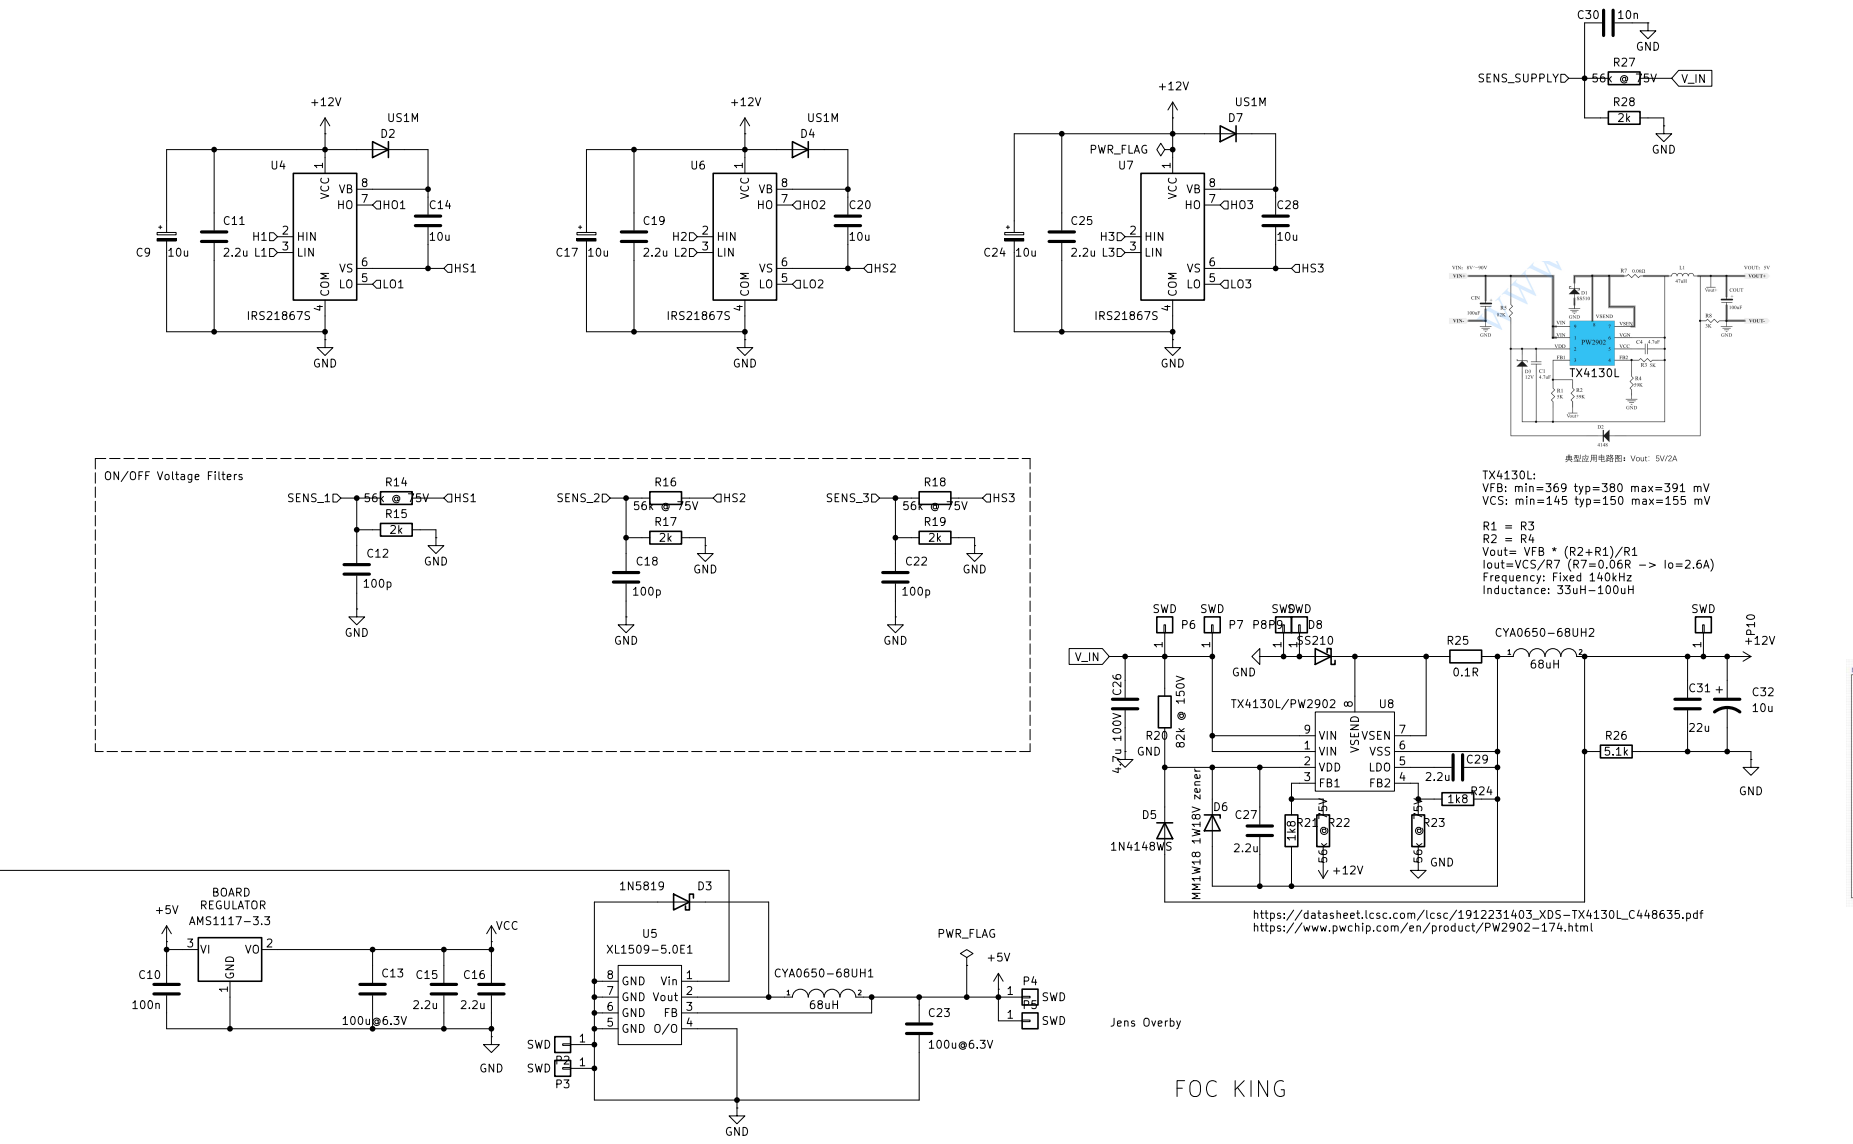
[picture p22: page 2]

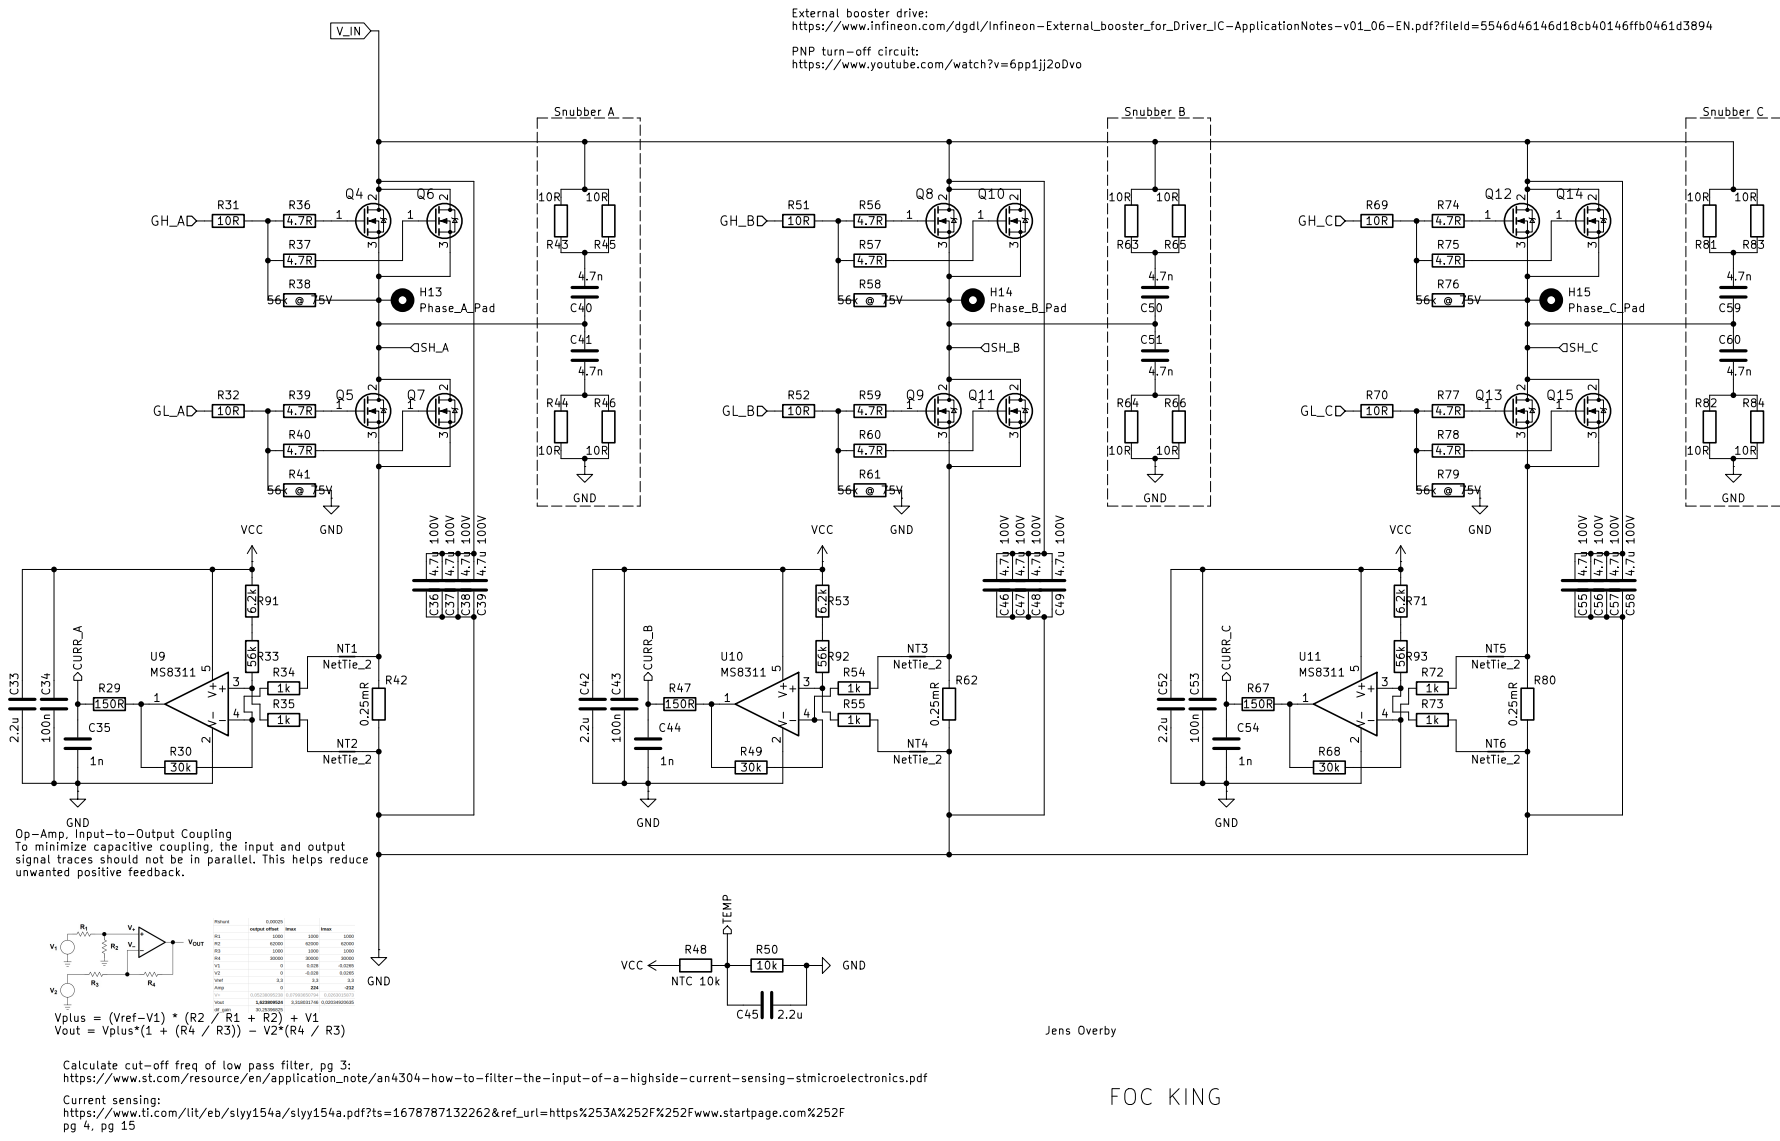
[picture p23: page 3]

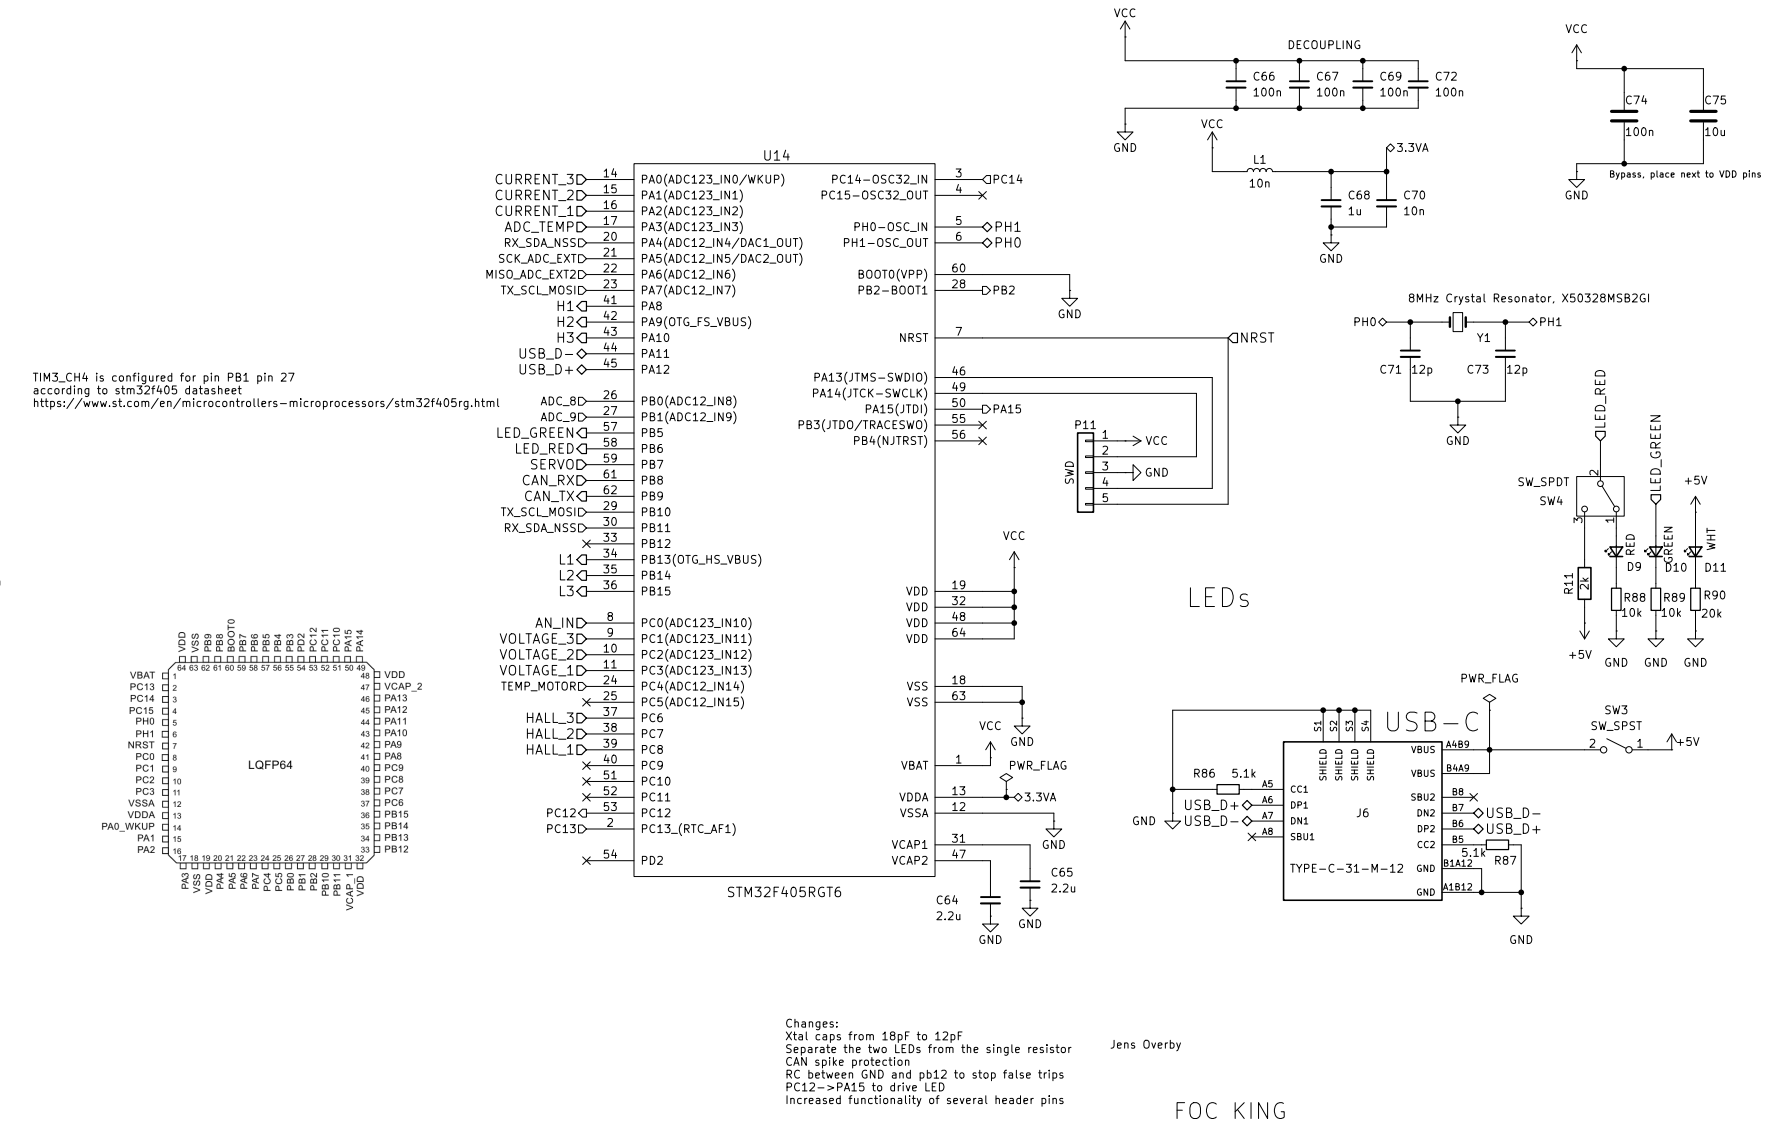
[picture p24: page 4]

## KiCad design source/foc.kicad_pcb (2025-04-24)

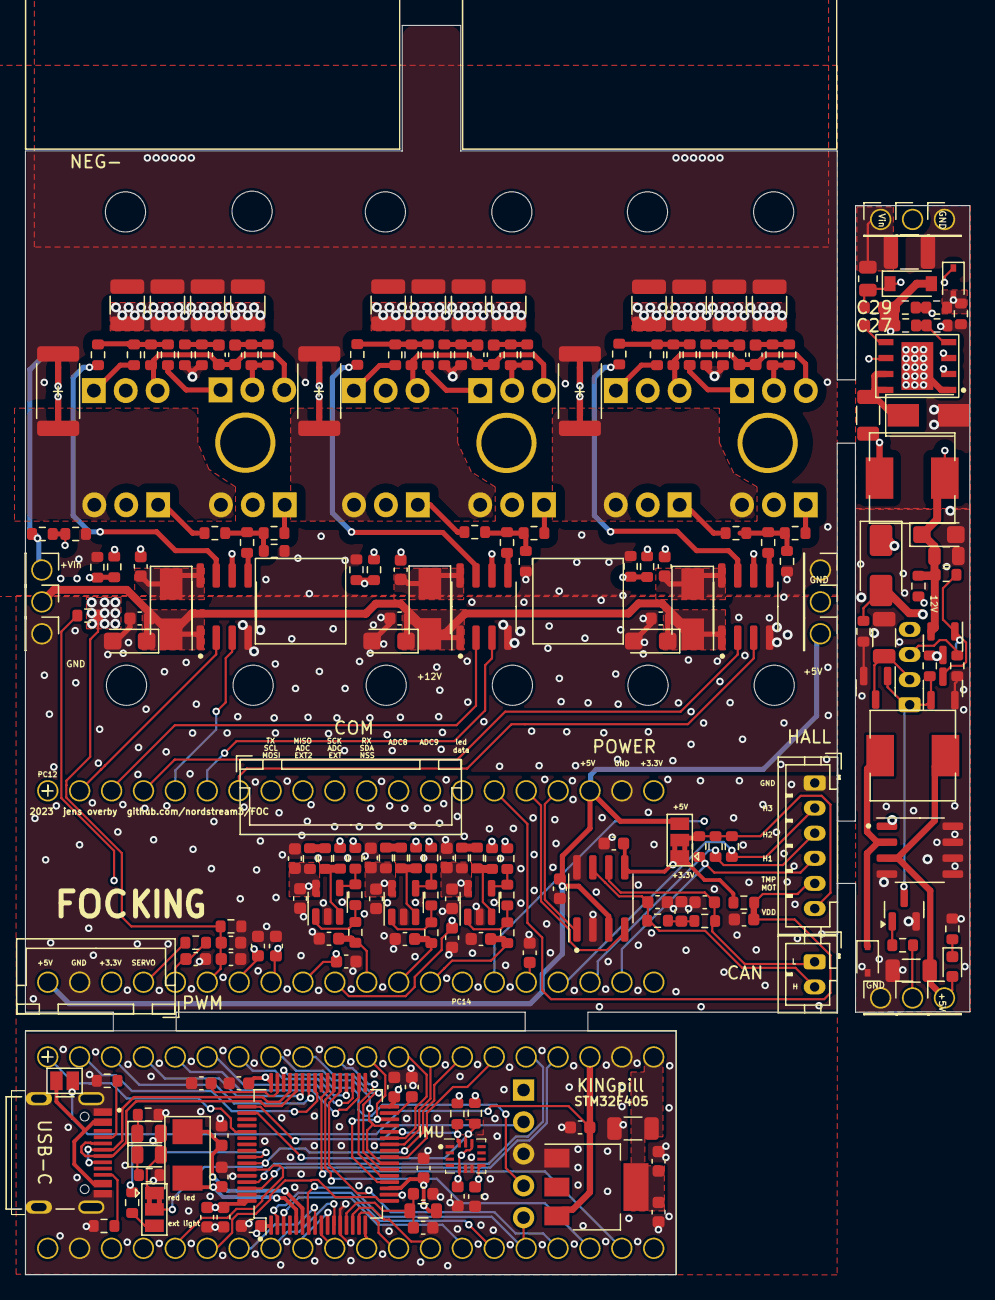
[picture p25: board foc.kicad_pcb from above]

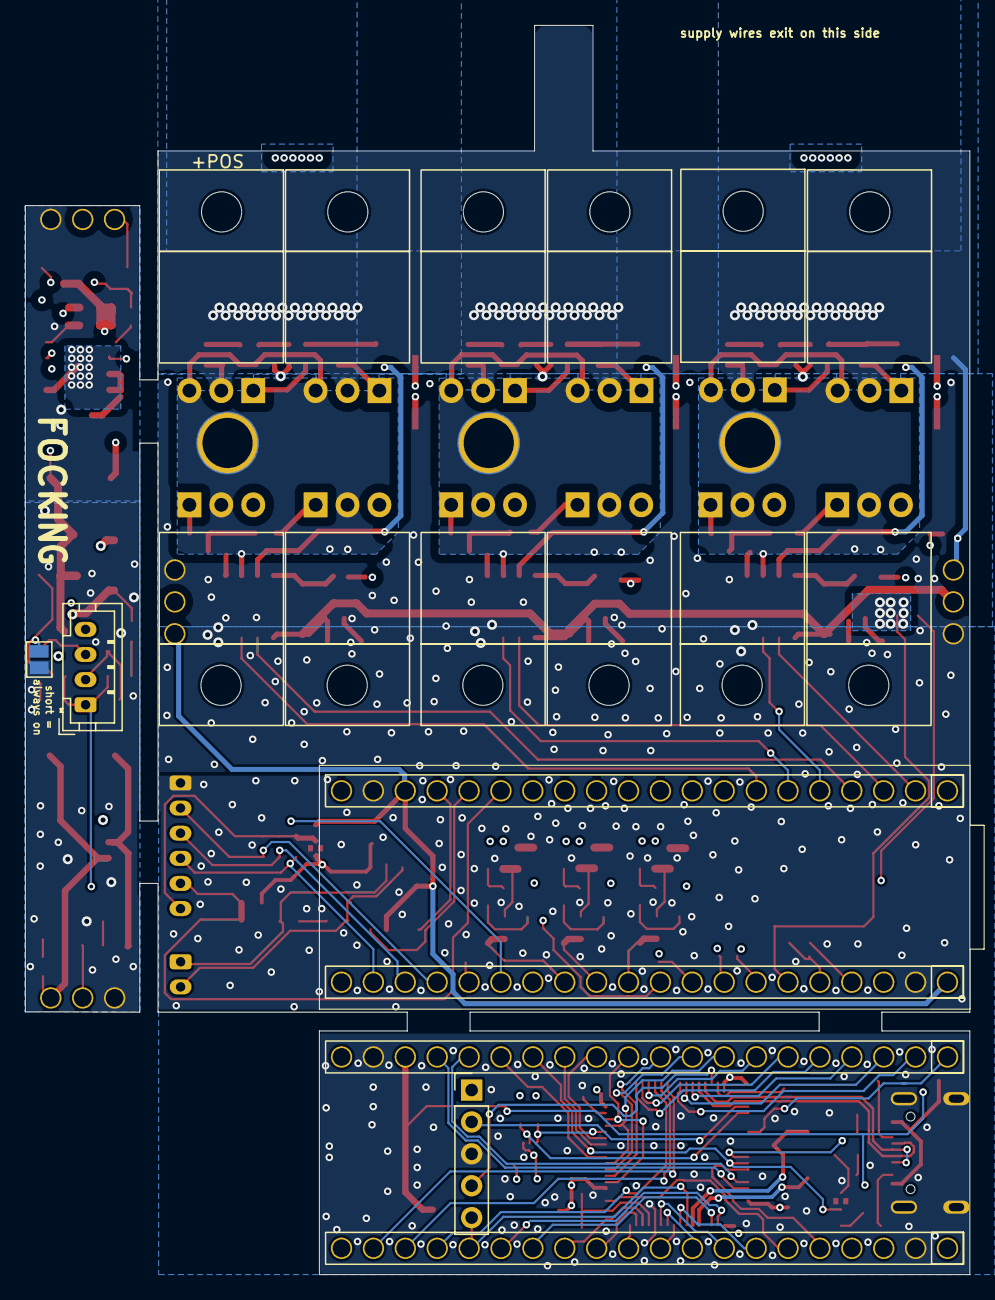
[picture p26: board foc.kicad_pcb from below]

Board: 4 copper layers, 75.2 x 99.5 mm, 259 parts (20 on the bottom side), 133 nets.

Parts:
C1, C40, C41, C50, C51, C59, C60: 4.7n; C_0603_1608Metric
C2, C3, C12, C18, C22: 100p; C_0603_1608Metric
C4, C7, C11, C15, C16, C19, C25, C27, C29, C33, C42, C45, C52, C64, C65: 2.2u; C_0603_1608Metric
C5, C6, C10, C21, C34, C43, C53, C61, C62, C63, C66, C67, C69, C72, C74: 100n; C_0603_1608Metric
C8, C13, C23: 100u@6.3V; C_1206_3216Metric
C9, C17, C24, C32: 10u; CP_EIA-3216-10_Kemet-I
C14, C20, C28, C75: 10u; C_0603_1608Metric
C26, C36, C37, C38, C39, C46, C47, C48, C49, C55, C56, C57, C58: 4.7u 100V; C_1210_3225Metric
C30, C70: 10n; C_0603_1608Metric
C31: 22u; C_0805_2012Metric
C35, C44, C54: 1n; C_0603_1608Metric
C68: 1u; C_0603_1608Metric
C71, C73: 12p; C_0603_1608Metric
CYA0650-68UH1, CYA0650-68UH2: 68uH; L_6.6x7.2_H5.0_CYA0650_68UH
D1, D2, D4, D7: US1M; D_SMA
D3: 1N5819; D_SOD-323
D5: 1N4148WS; D_SOD-323
D6: MM1W18 1W18V zener; D_SOD-123
D8: SS210; D_SMA
D9: RED; LED_0805_2012Metric
D10: GREEN; LED_0805_2012Metric
D11: WHT; LED_0603_1608Metric
H1, H2, H3, H4, H5, H6, H7, H8, H9, H10, H11, H12: MountingHole; MountingHole_3.2mm_M3
H13: Phase_A_Pad; MountingHole_3.5mm_Pad_TopOnly_custom
H14: Phase_B_Pad; MountingHole_3.5mm_Pad_TopOnly_custom
H15: Phase_C_Pad; MountingHole_3.5mm_Pad_TopOnly_custom
J1: Conn_01x02_Male; JST_PH_B2B-PH-K_1x02_P2.00mm_Vertical
J2: Conn_01x06; JST_PH_B6B-PH-K_1x06_P2.00mm_Vertical
J3: communication; JST_XH_B6B-XH-A_1x06_P2.50mm_Vertical
J4: on/off; JST_PH_B4B-PH-K_1x04_P2.00mm_Vertical
J5: servo; JST_XH_B4B-XH-A_1x04_P2.50mm_Vertical
J6: TYPE-C-31-M-12; HRO_TYPE-C-31-M-12
L1: 10n; L_0805_2012Metric
NT1, NT2, NT3, NT4, NT5, NT6: NetTie_2; NetTie-2_SMD_Pad0.5mm
P1, P2, P3, P4, P5, P6, P7, P8, P9, P10, P12, P13: SWD; PinHeader_1x01_P2.54mm_Vertical
P11: SWD; PinHeader_1x05_P2.54mm_Vertical
Q1: AO3401A; SOT-23
Q2, Q3, Q16: SS8050; SOT-23
Q4, Q5, Q6, Q7, Q8, Q9, Q10, Q11, Q12, Q13, Q14, Q15: CRST030N10N; TO-220-3_Vertical_bend
R1, R2, R3, R11, R15, R17, R19, R28: 2k; R_0603_1608Metric
R4, R5, R85: 100R; R_0603_1608Metric
R6, R13, R26, R86, R87: 5.1k; R_0603_1608Metric
R7, R10, R50, R88, R89: 10k; R_0603_1608Metric
R8, R9: 75k; R_0603_1608Metric
R12: 470k; R_0603_1608Metric
R14, R16, R18, R22, R23, R27, R38, R41, R58, R61, R76, R79: 56k @ 75V; R_0603_1608Metric
R20: 82k @ 150V; R_0805_2012Metric
R21, R24: 1k8; R_0603_1608Metric
R25: 0.1R; R_1206_3216Metric
R29, R47, R67: 150R; R_0603_1608Metric
R30, R49, R68: 30k; R_0603_1608Metric
R31, R32, R43, R44, R45, R46, R51, R52, R63, R64, R65, R66, R69, R70, R81, R82, R83, R84: 10R; R_0603_1608Metric
R33, R92, R93: 56k; R_0603_1608Metric
R34, R35, R54, R55, R72, R73, R96, R97: 1k; R_0603_1608Metric
R36, R37, R39, R40, R56, R57, R59, R60, R74, R75, R77, R78: 4.7R; R_0603_1608Metric
R42, R62, R80: 0.25mR; R_2512_6332Metric
R48: NTC 10k; R_0603_1608Metric
R53, R71, R91: 6.2k; R_0603_1608Metric
R90: 20k; R_0603_1608Metric
SW1, SW4: SW_SPDT; SolderJumper-3_P1.3mm_Bridged2Bar12_Pad1.0x1.5mm
SW2, SW3: SW_SPST; SolderJumper-2_P1.3mm_Open_Pad1.0x1.5mm
U1: TJA1051T/3/1J; SOIC-8_3.9x4.9mm_P1.27mm
U2: BMI270; Bosch_LGA-14_3x2.5mm_P0.5mm
U3: AMS1117-3.3; SOT-223-3_TabPin2
U4, U6, U7: IRS21867S; SOIC-8_3.9x4.9mm_P1.27mm
U5: XL1509-5.0E1; SOP-8_3.9x4.9mm_P1.27mm
U8: TX4130L/PW2902; TX4130L_ESOP-8
U9, U10, U11: MS8311; TSOT-23-5
U12, U13: STM32F401CCU6_Blackpill; Blackpill_STM32F401CEU6
U14: STM32F405RGT6; LQFP-64_10x10mm_P0.5mm
Y1: 8MHz Crystal Resonator, X50328MSB2GI; Crystal_SMD_5032-2Pin_5.0x3.2mm

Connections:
+5V: C4.1, C10.2, C23.1, CYA0650-68UH1.2, D11.2 (A), P4.1, P5.1, R11.1, SW1.3 (C), SW3.1 (A), U1.3 (VCC), U3.3 (VI), U5.3 (FB), U12.20 (5V), U12.38 (5V), U13.20 (5V), U13.38 (5V)
+12V: C9.1, C11.1, C17.1, C19.1, C24.1, C25.1, C31.1, C32.1, CYA0650-68UH2.2, D2.2 (A), D4.2 (A), D5.2 (A), D7.2 (A), P10.1, Q1.2 (S), R8.2, R12.2, R22.1, R26.2, U4.1 (VCC), U6.1 (VCC), U7.1 (VCC)
/driver/H1: U4.2 (HIN), U12.22 (PB13), U13.22 (PB13), U14.41 (PA8)
/driver/H2: U6.2 (HIN), U12.23 (PB14), U13.23 (PB14), U14.42 (PA9(OTG_FS_VBUS))
/driver/H3: U7.2 (HIN), U12.24 (PB15), U13.24 (PB15), U14.43 (PA10)
/driver/HO1: R31.2, U4.7 (HO)
/driver/HO2: R51.2, U6.7 (HO)
/driver/HO3: R69.2, U7.7 (HO)
/driver/HS1: C14.2, C40.1, C41.1, H13.1, Q4.3 (S), Q5.2 (D), Q6.3 (S), Q7.2 (D), R14.2, R38.1, U4.6 (VS)
/driver/HS2: C20.2, C50.1, C51.1, H14.1, Q8.3 (S), Q9.2 (D), Q10.3 (S), Q11.2 (D), R16.2, R58.1, U6.6 (VS)
/driver/HS3: C28.2, C59.1, C60.1, H15.1, Q12.3 (S), Q13.2 (D), Q14.3 (S), Q15.2 (D), R18.2, R76.1, U7.6 (VS)
/driver/L1: U4.3 (LIN), U12.25 (PA8), U13.25 (PA8), U14.34 (PB13(OTG_HS_VBUS))
/driver/L2: U6.3 (LIN), U12.26 (PA9), U13.26 (PA9), U14.35 (PB14)
/driver/L3: U7.3 (LIN), U12.27 (PA10), U13.27 (PA10), U14.36 (PB15)
/driver/LO1: R32.2, U4.5 (LO)
/driver/LO2: R52.2, U6.5 (LO)
/driver/LO3: R70.2, U7.5 (LO)
/driver/MCU_SHUTDOWN: P12.1, P13.1, R6.2, U12.6 (PA0), U13.6 (PA0), U14.2 (PC13_(RTC_AF1))
/driver/SENS_1: C12.2, R14.1, R15.1, U12.13 (PA7), U13.13 (PA7), U14.11 (PC3(ADC123_IN13))
/driver/SENS_2: C18.2, R16.1, R17.1, U12.12 (PA6), U13.12 (PA6), U14.10 (PC2(ADC123_IN12))
/driver/SENS_3: C22.2, R18.1, R19.1, U12.11 (PA5), U13.11 (PA5), U14.9 (PC1(ADC123_IN11))
/driver/SENS_SUPPLY: C30.1, R27.1, R28.1, U12.14 (PB0), U13.14 (PB0), U14.8 (PC0(ADC123_IN10))
/mcu/3.3VA: C68.1, C70.1, L1.2, U14.13 (VDDA)
/mcu/ADC_8: U12.33 (PB5), U13.33 (PB5), U14.26 (PB0(ADC12_IN8))
/mcu/ADC_9: U12.32 (PB4), U13.32 (PB4), U14.27 (PB1(ADC12_IN9))
/mcu/ADC_TEMP: C45.2, C62.1, R48.1, R50.2, U12.15 (PB1), U13.15 (PB1), U14.17 (PA3(ADC123_IN3))
/mcu/CAN_RX: U1.4 (RXD), U12.36 (PB8), U13.36 (PB8), U14.61 (PB8)
/mcu/CAN_TX: U1.1 (TXD), U12.37 (PB9), U13.37 (PB9), U14.62 (PB9)
/mcu/CURRENT_1: C35.1, R29.2, U12.10 (PA4), U13.10 (PA4), U14.16 (PA2(ADC123_IN2))
/mcu/CURRENT_2: C44.1, R47.2, U12.9 (PA3), U13.9 (PA3), U14.15 (PA1(ADC123_IN1))
/mcu/CURRENT_3: C54.1, R67.2, U12.8 (PA2), U13.8 (PA2), U14.14 (PA0(ADC123_IN0/WKUP))
/mcu/HALL_1: J2.4, R1.2, U12.2 (PC13), U13.2 (PC13), U14.39 (PC8)
/mcu/HALL_2: J2.3, R2.2, U12.3 (PC14), U13.3 (PC14), U14.38 (PC7)
/mcu/HALL_3: J2.2, R3.2, U12.4 (PC15), U13.4 (PC15), U14.37 (PC6)
/mcu/LED_GREEN: D10.2 (A), U14.57 (PB5)
/mcu/LED_RED: SW4.2 (B), U12.34 (PB6), U13.34 (PB6), U14.58 (PB6)
/mcu/MISO_ADC_EXT2: U12.29 (PA12), U13.29 (PA12), U14.22 (PA6(ADC12_IN6))
/mcu/NRST: C61.1, P11.5, U12.5 (NRST), U13.5 (NRST), U14.7 (NRST)
/mcu/PA15: R97.1, U2.13 (SCX), U14.50 (PA15(JTDI))
/mcu/PB2: R96.1, U2.14 (SDX), U14.28 (PB2-BOOT1)
/mcu/PC12: U12.21 (PB12), U13.21 (PB12), U14.53 (PC12)
/mcu/PC14: U12.7 (PA1), U13.7 (PA1), U14.3 (PC14-OSC32_IN)
/mcu/PH0: C71.1, U14.6 (PH1-OSC_OUT), Y1.1
/mcu/PH1: C73.1, U14.5 (PH0-OSC_IN), Y1.2
/mcu/RX_SDA_NSS: U12.31 (PB3), U13.31 (PB3), U14.20 (PA4(ADC12_IN4/DAC1_OUT)), U14.30 (PB11)
/mcu/SCK_ADC_EXT: U12.30 (PA15), U13.30 (PA15), U14.21 (PA5(ADC12_IN5/DAC2_OUT))
/mcu/SERVO: C63.1, R85.2, U12.16 (PB2), U13.16 (PB2), U14.59 (PB7)
/mcu/TEMP_MOTOR: C21.1, J2.5, R7.1, U12.35 (PB7), U13.35 (PB7), U14.24 (PC4(ADC12_IN14))
/mcu/TX_SCL_MOSI: U12.28 (PA11), U13.28 (PA11), U14.23 (PA7(ADC12_IN7)), U14.29 (PB10)
/mcu/USB_D+: J6.A6 (DP1), J6.B6 (DP2), U14.45 (PA12)
/mcu/USB_D-: J6.A7 (DN1), J6.B7 (DN2), U14.44 (PA11)
GND: C1.2, C2.2, C3.2, C4.2, C5.1, C6.1, C7.2, C8.2, C9.2, C10.1, C11.2, C12.1, C13.2, C15.1, C16.1, C17.2, C18.1, C19.2, C21.2, C22.1, C23.2, C24.2, C25.2, C26.1, C30.2, C31.2, C32.2, C33.2, C34.2, C35.2, C36.2, C37.2, C38.2, C39.2, C42.2, C43.2, C44.2, C45.1, C46.2, C47.2, C48.2, C49.2, C52.2, C53.2, C54.2, C55.2, C56.2, C57.2, C58.2, C61.2, C62.2, C63.2, C64.2, C65.2, C66.2, C67.2, C68.2, C69.2, C70.2, C71.2, C72.2, C73.2, C74.2, C75.2, D3.2 (A), D8.2 (A), J2.1, J6.A1B12 (GND), J6.B1A12 (GND), J6.S1 (SHIELD), J6.S2 (SHIELD), J6.S3 (SHIELD), J6.S4 (SHIELD), NT2.2, NT4.2, NT6.2, P2.1, P3.1, P8.1, P9.1, P11.3, Q2.2 (E), Q3.2 (E), Q16.2 (E), R10.2, R13.1, R15.2, R17.2, R19.2, R23.1, R26.1, R28.2, R41.1, R42.1, R44.2, R46.2, R50.1, R61.1, R62.1, R64.2, R66.2, R79.1, R80.1, R82.2, R84.2, R86.2, R87.2, R88.1, R89.1, R90.1, SW2.2 (B), U1.2 (GND), U1.8 (S), U2.1 (SDO), U2.6 (GNDIO), U2.7 (GND), U3.1 (GND), U4.4 (COM), U5.4 (O/O), U5.5 (GND), U5.6 (GND), U5.7 (GND), U5.8 (GND), U6.4 (COM), U7.4 (COM), U9.2 (V-), U10.2 (V-), U11.2 (V-), U12.19 (GND), U12.39 (GND), U13.19 (GND), U13.39 (GND), U14.12 (VSSA), U14.18 (VSS), U14.60 (BOOT0(VPP)), U14.63 (VSS)
unnamed: C1.1, R4.1, R5.2
unnamed: C40.2, R43.1, R45.1
unnamed: C41.2, R44.1, R46.1
unnamed: C50.2, R63.1, R65.1
unnamed: C51.2, R64.1, R66.1
unnamed: C59.2, R81.1, R83.1
unnamed: C60.2, R82.1, R84.1
unnamed: D1.2 (A), Q1.3 (D), R9.2, R13.2
unnamed: D1.1 (K), J4.4, P1.1, U5.1 (Vin)
unnamed: C14.1, D2.1 (K), U4.8 (VB)
unnamed: CYA0650-68UH1.1, D3.1 (K), U5.2 (Vout)
unnamed: C20.1, D4.1 (K), U6.8 (VB)
unnamed: C27.2, D5.1 (K), D6.1 (K), R20.1, U8.2 (VDD)
unnamed: C27.1, C29.2, CYA0650-68UH2.1, D6.2 (A), R21.1, R24.1, R25.1, U8.6 (VSS)
unnamed: C28.1, D7.1 (K), U7.8 (VB)
unnamed: D8.1 (K), R25.2, U8.7 (VSEN), U8.8 (VSEND)
unnamed: D9.2 (A), SW4.1 (A)
unnamed: D9.1 (K), R88.2
unnamed: D10.1 (K), R89.2
unnamed: D11.1 (K), R90.2
unnamed: C3.1, J1.1, R5.1, U1.6 (CANL)
unnamed: C2.1, J1.2, R4.2, U1.7 (CANH)
unnamed: J2.6, R1.1, R2.1, R3.1, SW1.2 (B)
unnamed: J4.1, Q2.1 (B), Q3.1 (B), Q16.3 (C), R9.1
unnamed: C8.1, J4.2, Q3.3 (C), R12.1
unnamed: J4.3, R10.1
unnamed: R85.1, U12.17 (PB10)
unnamed: J6.A5 (CC1), R86.1
unnamed: J6.B5 (CC2), R87.1
unnamed: NT1.1, R34.1
unnamed: NT2.1, R35.1
unnamed: NT3.1, R54.1
unnamed: NT4.1, R55.1
unnamed: NT5.1, R72.1
unnamed: NT6.1, R73.1
unnamed: P11.2, U14.49 (PA14(JTCK-SWCLK))
unnamed: P11.4, U14.46 (PA13(JTMS-SWDIO))
unnamed: Q1.1 (G), Q2.3 (C), R8.1, SW2.1 (A)
unnamed: Q4.1 (G), R36.1
unnamed: Q5.1 (G), R39.1
unnamed: NT1.2, Q5.3 (S), Q7.3 (S), R42.2
unnamed: Q6.1 (G), R37.1
unnamed: Q7.1 (G), R40.1
unnamed: Q8.1 (G), R56.1
unnamed: Q9.1 (G), R59.1
unnamed: Q10.1 (G), R57.1
unnamed: Q11.1 (G), R60.1
unnamed: NT3.2, Q9.3 (S), Q11.3 (S), R62.2
unnamed: Q12.1 (G), R74.1
unnamed: Q13.1 (G), R77.1
unnamed: NT5.2, Q13.3 (S), Q15.3 (S), R80.2
unnamed: Q14.1 (G), R75.1
unnamed: Q15.1 (G), R78.1
unnamed: Q16.1 (B), R6.1
unnamed: R29.1, R30.2, U9.1
unnamed: R31.1, R36.2, R37.2, R38.2
unnamed: R32.1, R39.2, R40.2, R41.2
unnamed: R33.2, R91.1
unnamed: R47.1, R49.2, U10.1
unnamed: R51.1, R56.2, R57.2, R58.2
unnamed: R52.1, R59.2, R60.2, R61.2
unnamed: R53.1, R92.2
unnamed: R67.1, R68.2, U11.1
unnamed: R69.1, R74.2, R75.2, R76.2
unnamed: R70.1, R77.2, R78.2, R79.2
unnamed: R71.1, R93.2
unnamed: J6.A4B9 (VBUS), J6.B4A9 (VBUS), SW3.2 (B)
unnamed: R11.2, SW4.3 (C)
unnamed: R21.2, R22.2, U8.3 (FB1)
unnamed: R23.2, R24.2, U8.4 (FB2)
unnamed: C29.1, U8.5 (LDO)
unnamed: R33.1, R35.2, U9.3 (+)
unnamed: R30.1, R34.2, U9.4 (-)
unnamed: R55.2, R92.1, U10.3 (+)
unnamed: R49.1, R54.2, U10.4 (-)
unnamed: R73.2, R93.1, U11.3 (+)
unnamed: R68.1, R72.2, U11.4 (-)
unnamed: C65.1, U14.31 (VCAP1)
unnamed: C64.1, U14.47 (VCAP2)
VCC: C5.2, C6.2, C7.1, C13.1, C15.2, C16.2, C33.1, C34.1, C42.1, C43.1, C52.1, C53.1, C66.1, C67.1, C69.1, C72.1, C74.1, C75.1, L1.1, P11.1, R7.2, R48.2, R53.2, R71.2, R91.2, R96.2, R97.2, SW1.1 (A), U1.5 (VIO), U2.5 (VDDIO), U2.8 (VDD), U2.12 (CSB), U3.2 (VO), U9.5 (V+), U10.5 (V+), U11.5 (V+), U12.18 (3V3), U12.40 (3V3), U13.18 (3V3), U13.40 (3V3), U14.1 (VBAT), U14.19 (VDD), U14.32 (VDD), U14.48 (VDD), U14.64 (VDD)
V_IN: C26.2, C36.1, C37.1, C38.1, C39.1, C46.1, C47.1, C48.1, C49.1, C55.1, C56.1, C57.1, C58.1, P6.1, P7.1, Q4.2 (D), Q6.2 (D), Q8.2 (D), Q10.2 (D), Q12.2 (D), Q14.2 (D), R20.2, R27.2, R43.2, R45.2, R63.2, R65.2, R81.2, R83.2, U8.1 (VIN), U8.9 (VIN)

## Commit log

2023-06-07 4 layer design
    [driver.kicad_sch, foc.kicad_pcb, foc.kicad_sch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]
2023-08-24 First 4 layer order at JLCPCB
    [driver.kicad_sch, foc.kicad_pcb, foc.kicad_sch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]
2023-10-06 Add files via upload
    Filter resistor on current op-amps changed from 30k to 150R
    Mosfets at 45 deg angle
    Changed layout of power supply
    Cut through center of board
    Unnecessary components near mosfets removed
    Voltage filters removed again
    Crystal suspected noise source - moved to back of board
    Current sensing moved to in0 - in2 (PA0-PA2)
    Voltage sensing moved to in11-in13
    Supply voltage moved to in10
    Mosfets can now be attached to heat-sink plate using screws (that can be tightened throug holes in the board)
    [driver.kicad_sch, foc.kicad_pcb, foc.kicad_sch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]
2023-10-17 2 board setup with mcu and foc shield separated
    [driver.kicad_sch, foc.kicad_sch, mcu.kicad_sch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]
2023-10-30 Add files via upload
    2 missing gnd connections on mcu
    missing gnd connection on 12V power supply
    pin4 pulled to gnd on 5V power supply
    [driver.kicad_sch, foc.kicad_sch, mcu.kicad_sch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]
2023-11-05 JLCPCB order with separate power supply
    [driver.kicad_sch, foc.kicad_sch, mcu.kicad_sch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]
2023-11-05 JLCPCB order with separate power supplty
2023-11-08 jlcpcb order
    [driver.kicad_sch, foc.kicad_sch, mcu.kicad_sch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]
2023-11-12 Add files via upload
    Bugs in the jlcbpcb order, so it was cancelled. This commit marks a new jlcpcb order.
    [mcu.kicad_sch]
2023-11-28 jlcpcb reorder of main-module only
    [driver.kicad_sch, foc.kicad_sch, mcu.kicad_sch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]
2023-12-17 Add files via upload
    Added six pull down resistors to mosfet gates, and removed 100 pF filter caps on current samplings. Changed Logo back to FOC-king. This is a potential release candidates - everything works, also HFI.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
    [driver.kicad_sch, foc.kicad_sch, mcu.kicad_sch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]
2024-01-03 Moved traces to make peripherals work
    PPM now works -> moved trace to PB7
    UART works -> connected PB10 and PB11 to Communication port (like vesc 75_300 UART)
    Removed NRF24 pinheader
    Added motor_temperature to Hall pinheader, like it should be
    [driver.kicad_sch, foc.kicad_sch, mcu.kicad_sch]
2024-01-03 Pcb order as of 01.03.24
    [bom.csv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]
2024-01-12 CAN without 5V
    [bom.csv]
2024-02-02 Add files via upload
    LCSC number for 330uF is now correct
    [power.kicad_sch]
2024-03-20 Momentary switch
2024-03-22 Yellow LED resistor from 10k to 5k
    [bom.csv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]
2025-03-11 New bosch IMU, automatic shutdown, momentary sw.
    [driver.kicad_sch, foc.kicad_sch, mcu.kicad_sch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]
2025-03-11 Create vesc_source_code
2025-04-24 DRC run
    [foc.kicad_pcb]
2025-04-24 Using jlcpcb fabrication plugin
    [bom.csv, positions.csv]
